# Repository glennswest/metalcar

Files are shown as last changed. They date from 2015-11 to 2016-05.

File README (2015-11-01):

Kossel Metal Car Carriage

Im in the process of building a full metal Kossel 3d Printer. 
I've already fabbed metal corners, and want to do carriage and effector in metal. 
This is my current work in progress for the carriage. 
Its designed for 3 wheels from openbuilds, and a ecentric spacer for tension.
The car usings a iron cup and a rare earth magnet. 
The cup is threaded from the rear for a m3 screw. 
The upwards retangular is designed for mounting of a magnet, 
or with tape a flag for optical, or to push a switch.

BOM and Assembly
One Car consists of

Qty Description URL
3 Delrin V Wheel Kit http://openbuildspartstore.com/delrin-v-wheel-kit/
1 Ecentric Spacer http://openbuildspartstore.com/eccentric-spacer/
2 Magnetic Can Coming Soon from NCC
2 Magnets Coming Soon from NCC
2 M3 Screws For Mounting mag cups
2 M3 Grub Screws For Mounting Magnets

You need 3 sets of the above for a Kossel Printer

Thingiverse
http://www.thingiverse.com/thing:1103967

Using a CNC to Create:
CNC Workflow:
    Create part in openscad - Finish with a projection, and export to svg
    open JScut in your web browser (http://jscut.org)
    Setup your tool sizes (I use a 1mm bit)
    Setup your PX to Inch to 26.74
    Setup how thick you want to cut (6mm for dibond for me)
    Select the object
    Generate a outside cut
    Save to ChilliPeppr via gdrive
    Switch to http://chilipeppr.com/tinyg
    Load the gcode using the jscut via gdrive
    Preview to make sure it looks right
    Start Cutting

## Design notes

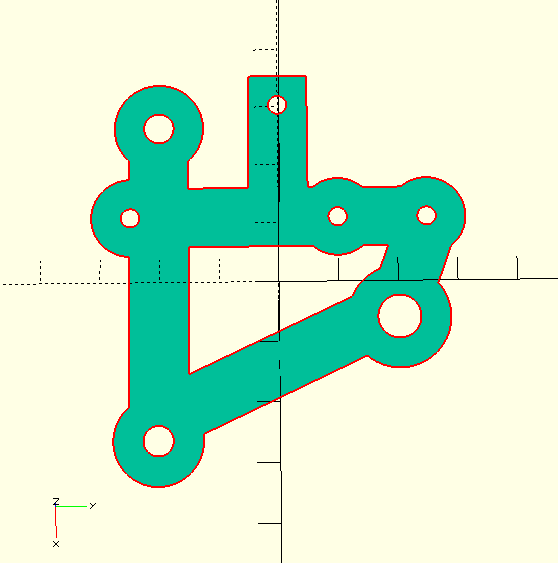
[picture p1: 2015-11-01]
metalcar.png

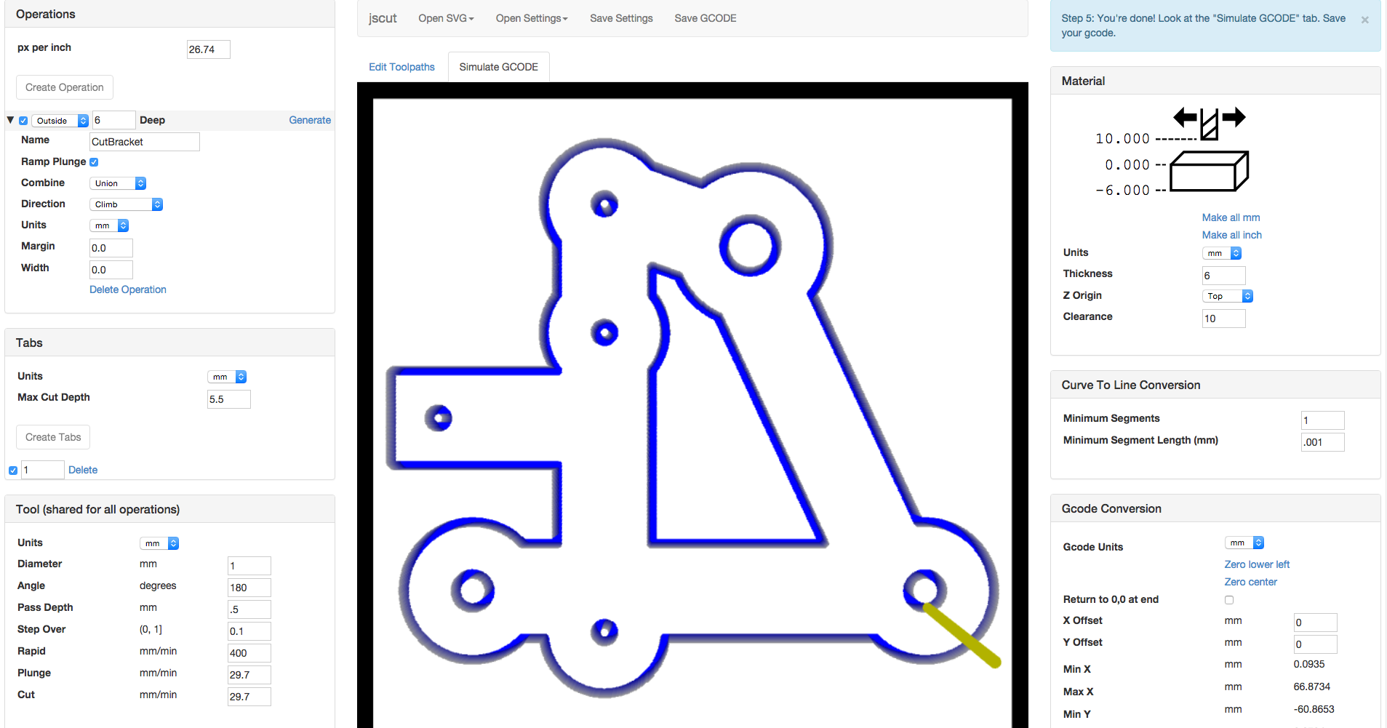
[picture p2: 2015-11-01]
jscut-settings.png

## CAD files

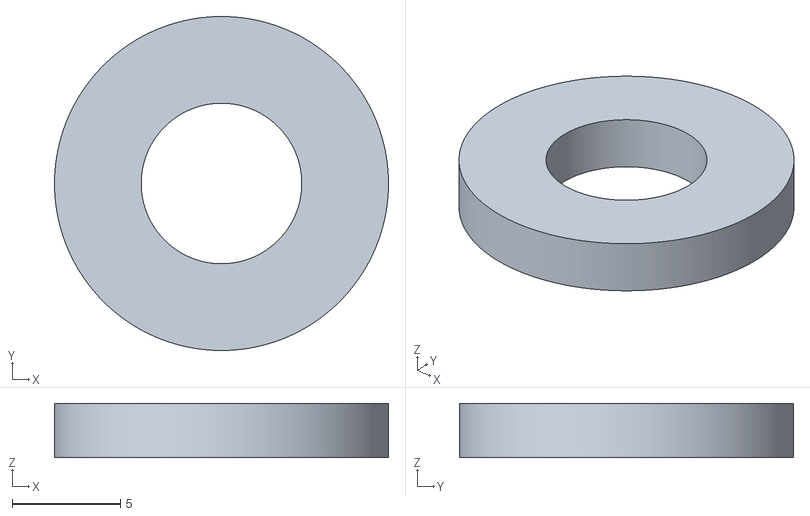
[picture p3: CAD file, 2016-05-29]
etest.stl
15.4 x 15.4 x 2.50

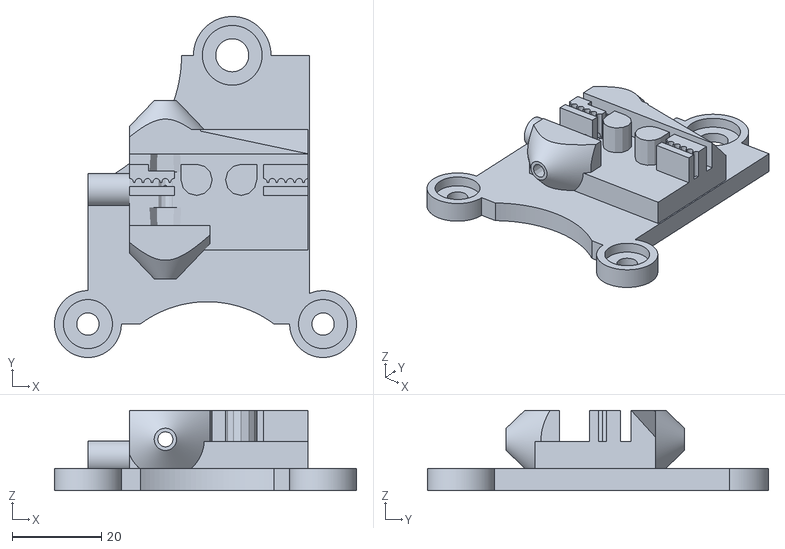
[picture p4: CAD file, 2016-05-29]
metalcar40.stl
67.8 x 76.5 x 18.0

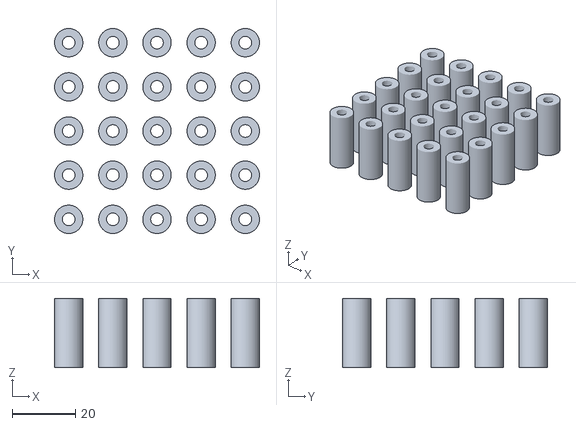
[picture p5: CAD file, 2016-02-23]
spacer22.stl
65.0 x 65.0 x 22.0

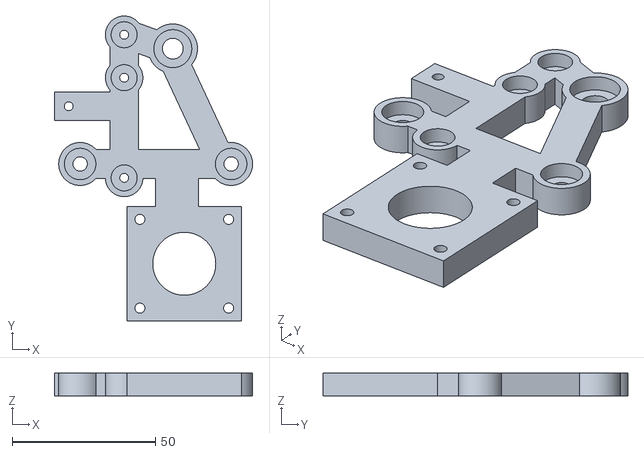
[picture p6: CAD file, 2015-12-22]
metalcar_stepper_prt.stl
69.2 x 106.5 x 8.00

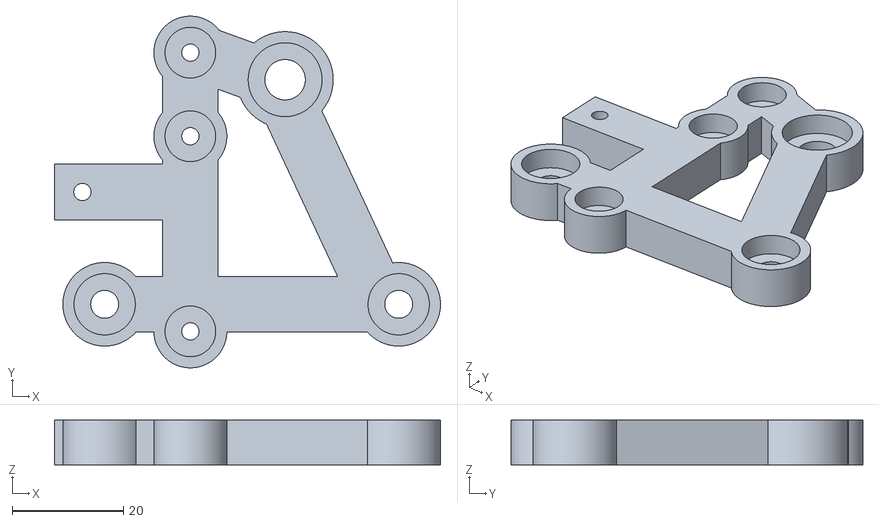
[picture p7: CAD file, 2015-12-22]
metalcar_prt.stl
69.2 x 63.1 x 8.00

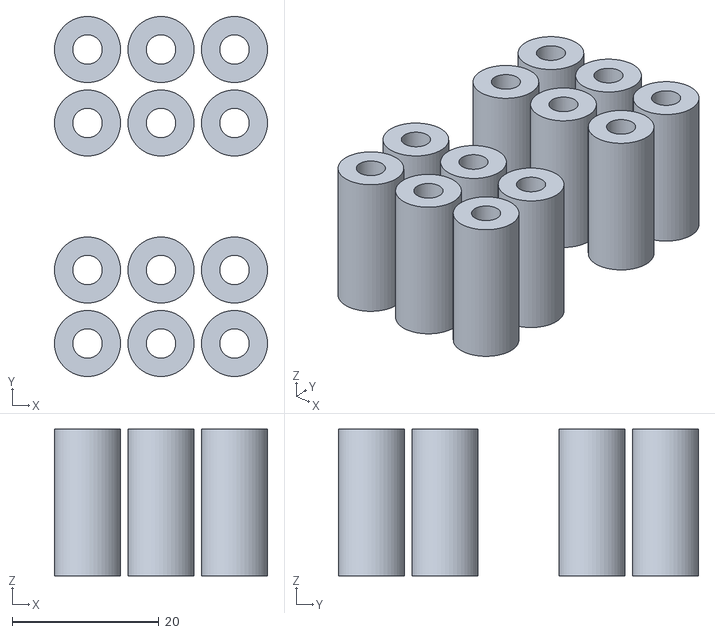
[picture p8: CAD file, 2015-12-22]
spacer.stl
29.0 x 49.0 x 20.0

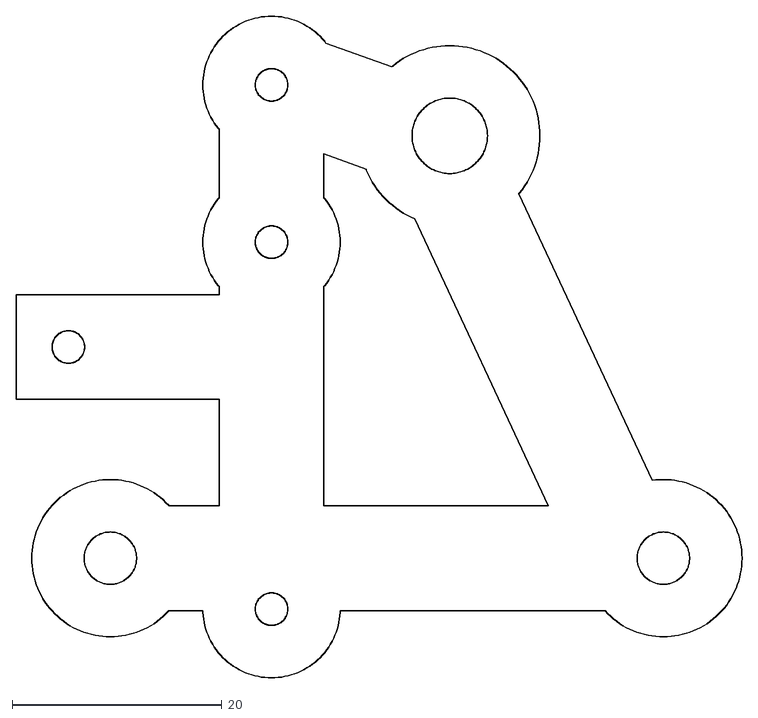
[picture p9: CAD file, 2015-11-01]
metalcar.dxf
69.2 x 63.1

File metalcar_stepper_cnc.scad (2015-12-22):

use <metalcar.scad>


projection(cut=true) metalcar(0,1);

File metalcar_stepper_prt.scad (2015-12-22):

use <metalcar.scad>

translate([0,0,0]) metalcar(0,1);
translate([0,0,4]) metalcar(3,1);

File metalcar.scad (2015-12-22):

include <MCAD/motors.scad>

yspacing = 40.29;
xspacing = 52.75;
halfx = xspacing / 2;
halfy = yspacing / 2;
$fn=128;

magspacing = 50;
halfmag = magspacing / 2;
theheight = 4;

module theholes(extra=0)
{
    translate([0-halfx,0-halfy,0]) cylinder(r=2.5+extra,h=theheight);
    translate([0+halfx,0-halfy,0]) cylinder(r=2.5+extra,h=theheight);
    translate([6,0+halfy,0]) cylinder(r=3.625+extra,h=theheight);
    
    // Mags
    translate([-11,0-halfmag,0]) cylinder(r=1.55+extra,h=theheight);
    translate([-11,0+halfmag,0]) cylinder(r=1.55+extra,h=theheight);
    
    // Belt
   translate([-11,0+halfmag-15,0]) cylinder(r=1.55+extra,h=theheight);
    
   translate([0-halfx-4,0,0]) cylinder(r=1.55,h=theheight);
}

module body_stepper()
{
difference(){
        translate([-10,-75,0]) cube([40,40,theheight]);
        translate([10,-55,-.1]) linear_extrude(height=theheight+.2) stepper_motor_mount(17,mochup=false);
        }    
       translate([0,-40,0]) cube([15,20,theheight]);   
}

module body(stepper=0)
{
    if (stepper==1) body_stepper();
    
    translate([0-halfx-9,-5,0]) cube([20,10,theheight]);
    translate([0-halfx,0-halfy-5,0]) cube([xspacing,10,theheight]);
    translate([-11-5,0-halfmag,0]) cube([10,magspacing,theheight]);
    translate([20,0-halfmag,0]) rotate([0,0,25]) cube([10,magspacing,theheight]);
    translate([6-3,0+halfy-5,0]) rotate([0,0,70]) cube([10,20,theheight]); 
    theholes(5);  
}



module metalcar(extra,stepper)
{
    difference(){
        body(stepper);
        theholes(extra);
    }
}

translate([0,0,0]) metalcar(0,0);
translate([0,0,theheight]) metalcar(3,0);

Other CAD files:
metalcar40.scad
etest.scad
metalcar_cnc.scad
metalcar_prt.scad
spacer.scad
spacer22.scad

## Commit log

2015-11-01 Cleanup vertical bar
    [metalcar.dxf, metalcar.scad]
2015-11-01 Fix px to inch settings
    [cube.scad]
2015-12-22 Added 4 file breakout
    [cube.scad, metalcar.scad, metalcar.stl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]
2016-02-23 Add spacer22
    [spacer22.scad, spacer22.stl]
2016-05-29 Add metalcar40 - 4040 2040 compatible carriage
    [etest.scad, etest.stl, metalcar40.scad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]
